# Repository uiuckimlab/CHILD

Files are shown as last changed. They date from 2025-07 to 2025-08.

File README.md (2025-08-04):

## Overview
For hardware details, please refer to the [BOM](./hardware/BOM.md).  
For software installation, please refer to [Teleop_Instruction](./Teleop_Instruction.md).
## To-Do
- \[ \] Release assembly guide.

## Citation
If you find this code useful in your research, please consider citing:
```
@article{child,
    title={CHILD (Controller for Humanoid Imitation and Live Demonstration): a Whole-Body Humanoid Teleoperation System}, 
    author={Noboru Myers and Obin Kwon and Sankalp Yamsani and Joohyung Kim},
    year={2025},
    journal={arXiv preprint arXiv:2508.00162},
    url={https://arxiv.org/abs/2508.00162}, 
}
```

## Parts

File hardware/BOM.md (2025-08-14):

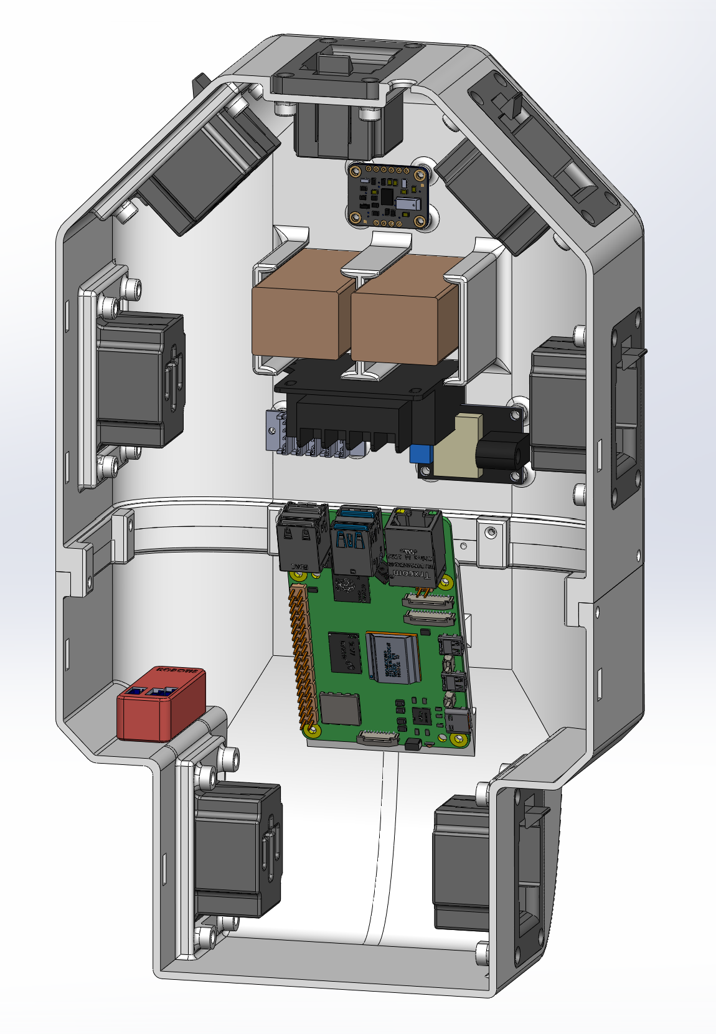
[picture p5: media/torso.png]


# Schematic
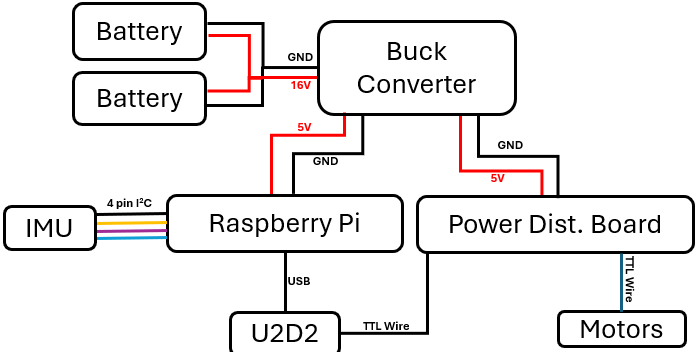
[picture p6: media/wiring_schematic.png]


# BOM
| Item | Quantity | Unit Cost (USD) | Cost | Source |  
| :--- | :---: | :---: | :---| :---|
| XL330-M288-T | 22 |  26.29 | 578.38 | [ROBOTIS](https://www.robotis.us/dynamixel-xl330-m288-t/)|
| XL330-M077-T | 2  |  26.29 | 52.58 | [ROBOTIS](https://www.robotis.us/dynamixel-xl330-m077-t/)|
| FPX330-H101 4pcs Set | 3  |  11.27 | 33.81 | [ROBOTIS](https://www.robotis.us/fpx330-h101-4pcs-set/)|
| Raspberry Pi 5a | 1  |  80 | 80 | [Digikey](https://www.digikey.com/en/products/detail/raspberry-pi/SC1112/21658257)|
| Raspberry Pi 5 active cooler | 1  |  9.50 | 9.50 | [Sparkfun](https://www.sparkfun.com/raspberry-pi-active-cooler.html?src=raspberrypi)|
| Buck converter | 1  |  11.00 | 11.00 | [Amazon](https://a.co/d/34K1G3W)|
| Lipo batteries | 2  |  31.49 | 62.98 | [getfpv](https://www.getfpv.com/batteries/mini-quad-batteries/lumenier-850mah-4s-75c-lipo-battery-xt-30.html)|
| IMU | 1  |  34.95 | 34.95 | [Adafruit](https://www.adafruit.com/product/2472)|
| U2D2 | 1  |  35.31 | 35.31 | [ROBOTIS](https://www.robotis.us/u2d2/?srsltid=AfmBOopnAfcYD4wZJd2mYGfl02LkN3lmzDXwg2oOkg-FG9G7V-jAIUyt)|
| TTL Expansion Board | 2  |  3.85 | 7.70 | [ROBOTIS](https://www.robotis.us/3p-extension-pcb/?searchid=199934&search_query=6+port+)|
| Baby Carrier | 1  |  37.99 | 37.99 | [Amazon](https://a.co/d/6YLBBi4)|
| XT30 Connector Female | 1  |  8.99 | 8.99 | [Amazon](https://a.co/d/beCXKoa)|
| SD card | 1  |  14.99 | 14.99 | [Amazon](https://a.co/d/bTOPJQl)|
| M3x8 screw | 33 |  0.0545 | 1.80 | [Mcmaster](https://www.mcmaster.com/91292A112/) |
| M2x8 screw | 4  |  0.0712 | 0.28 | [Mcmaster](https://www.mcmaster.com/91292a832/) |
| M2x6 screw | 24 |  0.0878 | 2.11 | [Mcmaster](https://www.mcmaster.com/91292a831/) |
| Female jumper wires | 6  |  0.0582 | 0.46 | [Amazon](https://a.co/d/gtiBsbT)|
| PLA Filament | 1.1kg  |  - | 25.3 | |
| | |  **Total** | 998.13 | |
### Miscellaneous
- Power wires

# Torso
**3D Prints**
- [leader_mount.STL](./3D_print_parts/leader_mount.STL) `x7`
- [back_cover_clip.STL](./3D_print_parts/back_cover_clip.STL) `x2`
- [back_cover_lower.STL](./3D_print_parts/back_cover_lower.STL)
- [back_cover_upper.STL](./3D_print_parts/back_cover_upper.STL)
- [torso_lower.STL](./3D_print_parts/torso_lower.STL)
- [torso_upper.STL](./3D_print_parts/torso_upper.STL)

# G1 Limb Leaders
Screws and wires for leader assembly (included in XL330 servo box):
- M2x6mm self tapping screw
- M2x8mm self tapping screw
- TTL wires

**3D Prints**
- [G1_Arm_Leader_R_handle.STL](./3D_print_parts/G1_Arm_Leader_R_handle.STL) `x2`
- [G1_Arm_Leader_trigger.STL](./3D_print_parts/G1_Arm_Leader_trigger.STL) `x2`
- [G1_Leg_Leader_foot.STL](./3D_print_parts/G1_Leg_Leader_foot.STL) `x2`
- [G1_Leg_Leader_knee_jnt_limit.STL](./3D_print_parts/G1_Leg_Leader_knee_jnt_limit.STL) `x2`
- [G1_Leg_Leader_link_2.STL](./3D_print_parts/G1_Leg_Leader_link_2.STL) `x2`
- [G1_Leg_Leader_link_3.STL](./3D_print_parts/G1_Leg_Leader_link_3.STL) `x2`
- [G1_Leg_Leader_link_4.1.STL](./3D_print_parts/G1_Leg_Leader_link_4.1.STL) `x2`
- [G1_Leg_Leader_link_4.2.STL](./3D_print_parts/G1_Leg_Leader_link_4.2.STL) `x2`
- [G1_Leg_Leader_L_link1.STL](./3D_print_parts/G1_Leg_Leader_L_link1.STL)
- [G1_Leg_Leader_R_link1.STL](./3D_print_parts/G1_Leg_Leader_R_link1.STL)
- [G1_Arm_Leader_L_link_1.STL](./3D_print_parts/G1_Arm_Leader_L_link_1.STL)
- [G1_Arm_Leader_L_link_2.STL](./3D_print_parts/G1_Arm_Leader_L_link_2.STL)
- [G1_Arm_Leader_L_link_3.STL](./3D_print_parts/G1_Arm_Leader_L_link_3.STL)
- [G1_Arm_Leader_L_link_4.STL](./3D_print_parts/G1_Arm_Leader_L_link_4.STL)
- [G1_Arm_Leader_L_link_5.STL](./3D_print_parts/G1_Arm_Leader_L_link_5.STL)
- [G1_Arm_Leader_L_link_6.STL](./3D_print_parts/G1_Arm_Leader_L_link_6.STL)
- [G1_Arm_Leader_R_link_1.STL](./3D_print_parts/G1_Arm_Leader_R_link_1.STL)
- [G1_Arm_Leader_R_link_2.STL](./3D_print_parts/G1_Arm_Leader_R_link_2.STL)
- [G1_Arm_Leader_R_link_3.STL](./3D_print_parts/G1_Arm_Leader_R_link_3.STL)
- [G1_Arm_Leader_R_link_4.STL](./3D_print_parts/G1_Arm_Leader_R_link_4.STL)
- [G1_Arm_Leader_R_link_5.STL](./3D_print_parts/G1_Arm_Leader_R_link_5.STL)
- [G1_Arm_Leader_R_link_6.STL](./3D_print_parts/G1_Arm_Leader_R_link_6.STL)

## Monitor Stand Adapter
- [Monitor_stand_attachment.STL](./3D_print_parts/Monitor_stand_attachment.STL)
- [Monitor_stand_bracket.STL](./3D_print_parts/Monitor_stand_bracket.STL)
- [monitor_stand_lock.STL](./3D_print_parts/monitor_stand_lock.STL)

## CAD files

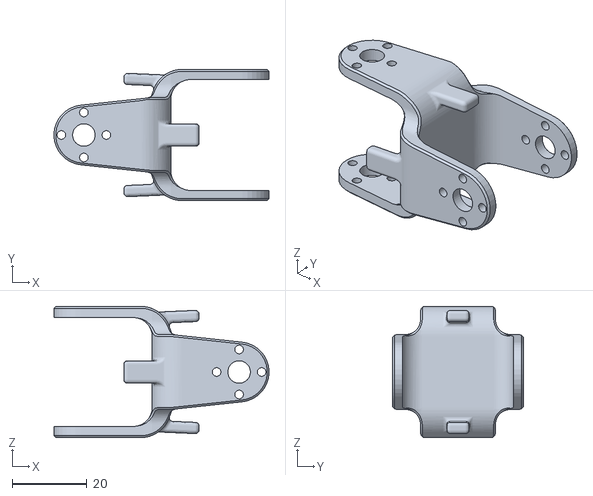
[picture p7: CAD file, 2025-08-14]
hardware/3D_print_parts/G1_Arm_Leader_L_link_6.STL
57.3 x 35.0 x 35.0

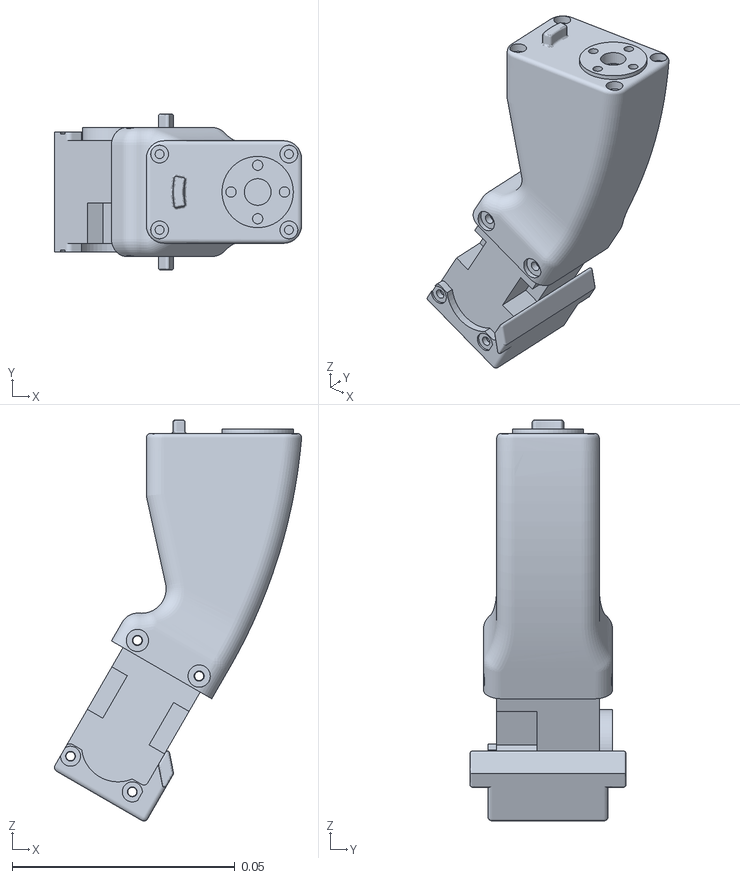
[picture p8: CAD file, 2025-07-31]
hw_interface/teleop_leaders/description/urdf/child_leaders/meshes/g1_leg_link_3.STL
0.0554 x 0.035 x 0.09

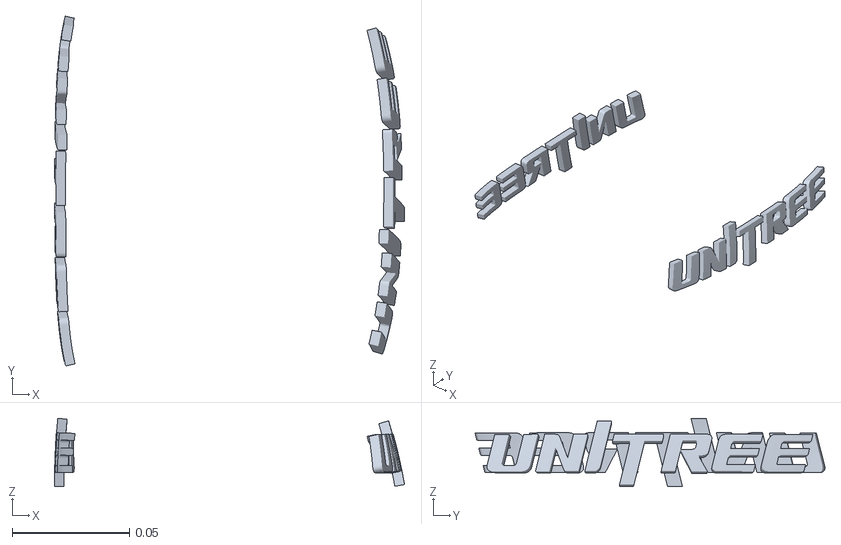
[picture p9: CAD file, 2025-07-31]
teleop_sw/models/assets/g1/meshes/logo_link.STL
0.149 x 0.149 x 0.0292

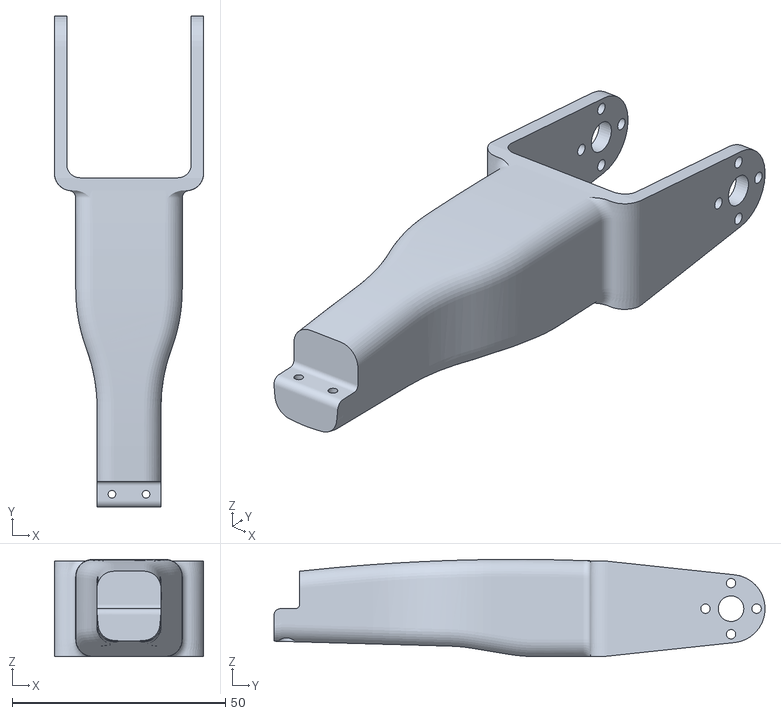
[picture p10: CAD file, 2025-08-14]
hardware/3D_print_parts/G1_Leg_Leader_link_4.1.STL
35.0 x 115.3 x 22.8

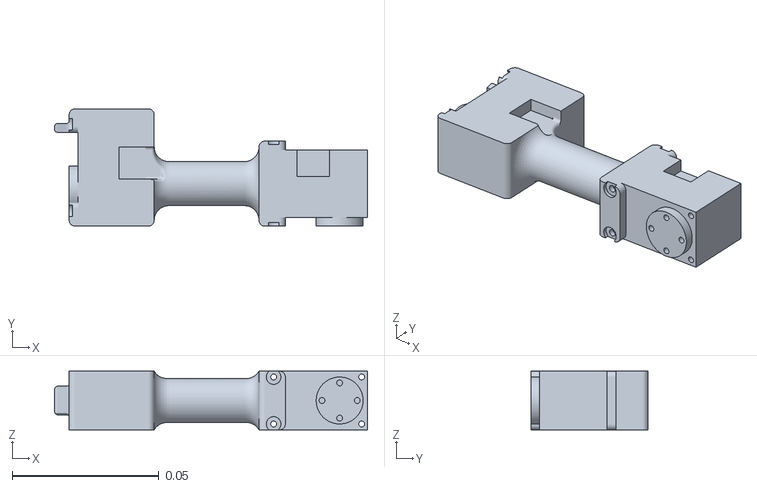
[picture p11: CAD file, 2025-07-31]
hw_interface/teleop_leaders/description/urdf/child_leaders/meshes/g1_arm_link_5_L.STL
0.107 x 0.04 x 0.02

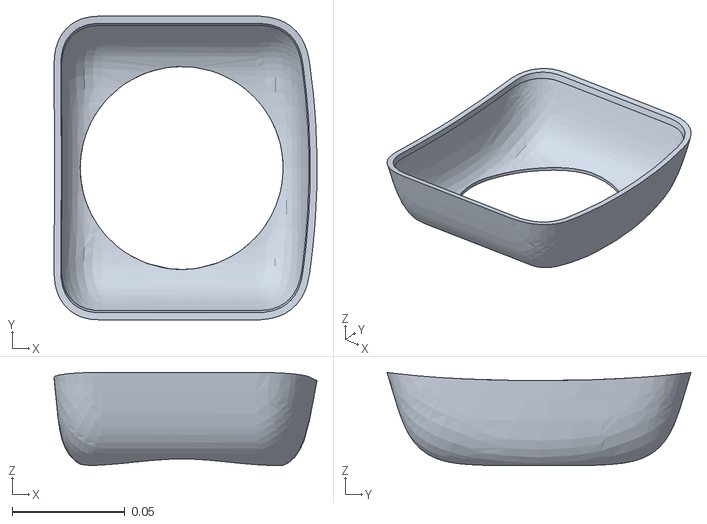
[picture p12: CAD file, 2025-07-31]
teleop_sw/models/assets/g1/meshes/waist_support_link.STL
0.117 x 0.135 x 0.0413

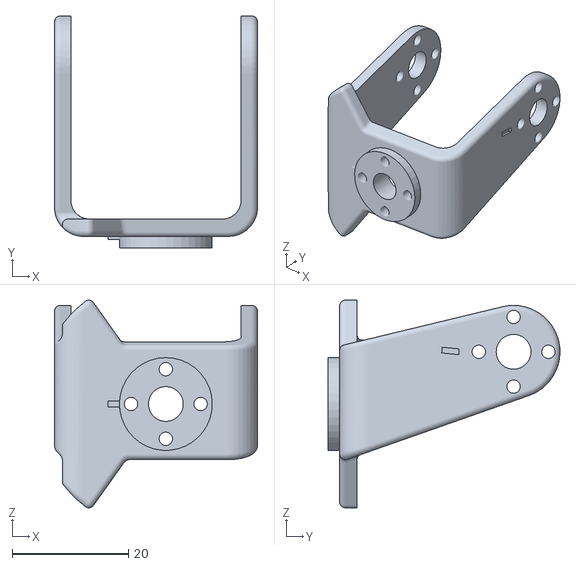
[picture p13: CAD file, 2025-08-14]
hardware/3D_print_parts/G1_Arm_Leader_L_link_4.STL
35.0 x 40.0 x 35.8

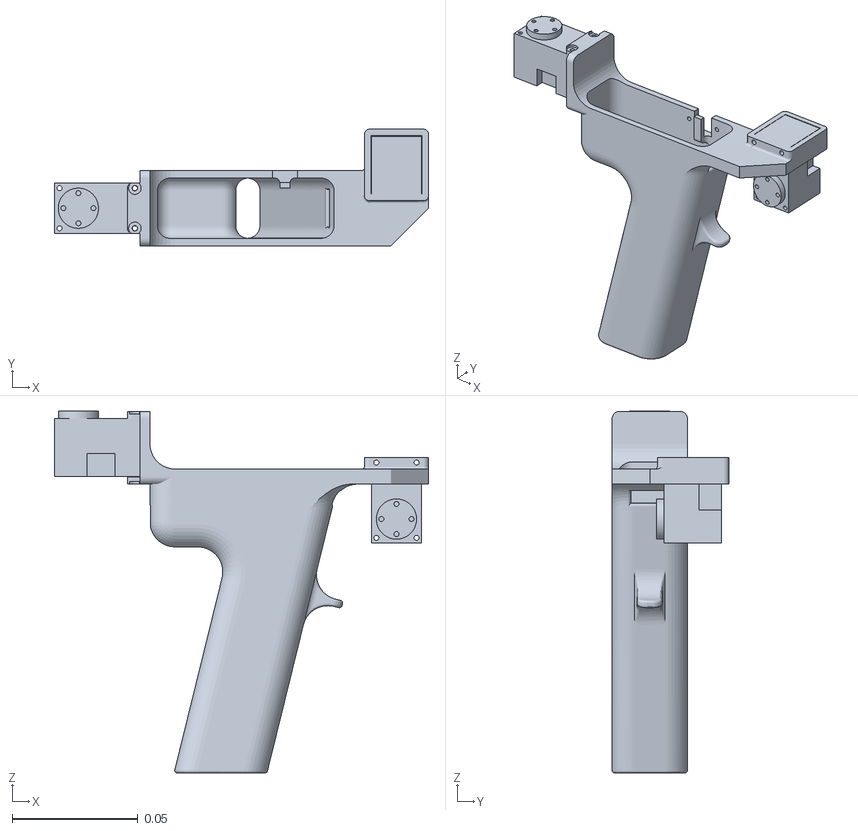
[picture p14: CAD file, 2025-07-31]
hw_interface/teleop_leaders/description/urdf/child_leaders/meshes/g1_arm_link_7_R.STL
0.149 x 0.0465 x 0.144

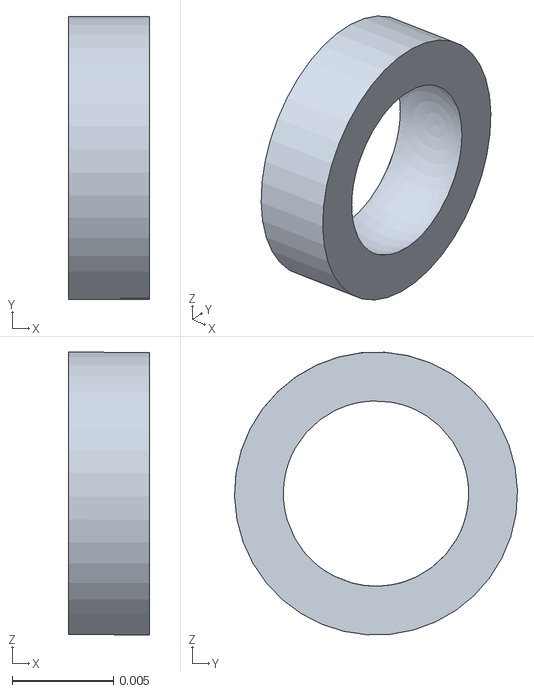
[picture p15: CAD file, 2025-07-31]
teleop_sw/models/assets/g1/meshes/torso_constraint_R_rod_link.STL
0.00401 x 0.014 x 0.014

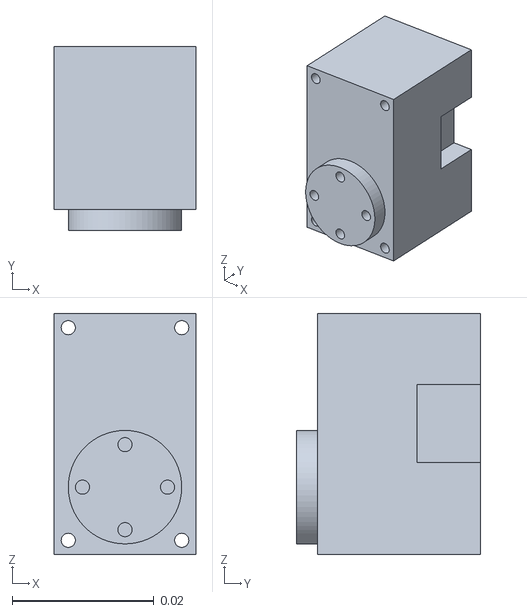
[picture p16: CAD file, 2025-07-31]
hw_interface/teleop_leaders/description/urdf/child_leaders/meshes/base_link_R.STL
0.02 x 0.026 x 0.034

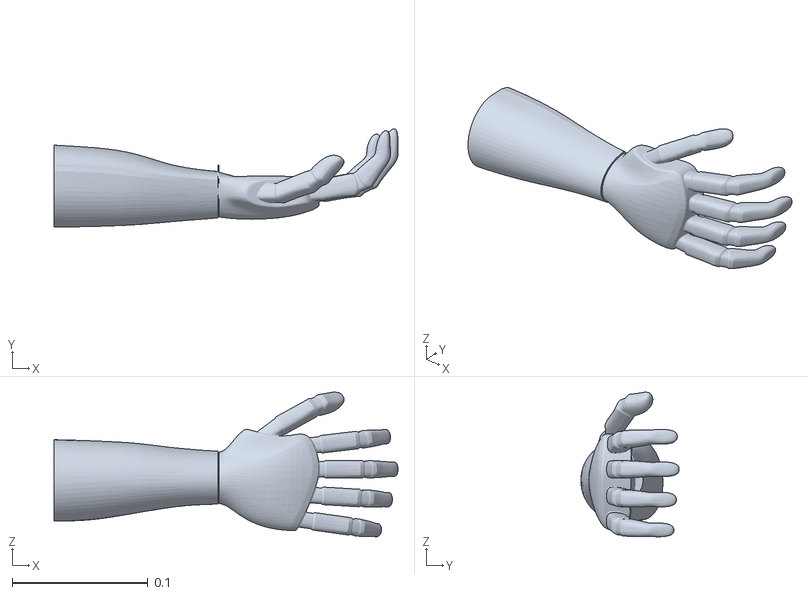
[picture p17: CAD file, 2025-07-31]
teleop_sw/models/assets/g1/meshes/right_wrist_roll_rubber_hand.STL
0.253 x 0.0724 x 0.106

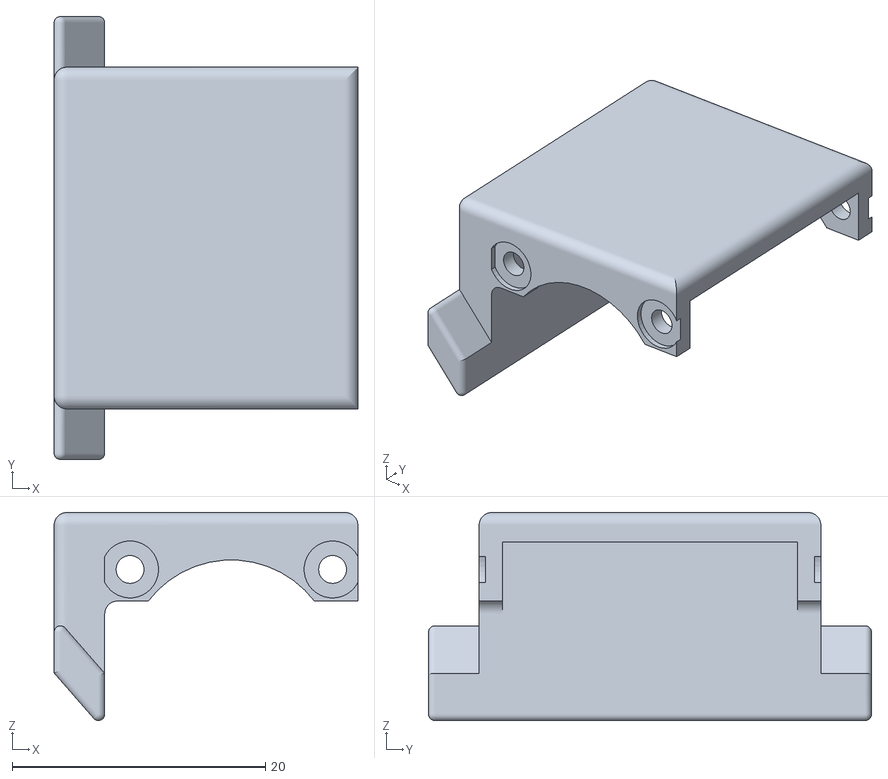
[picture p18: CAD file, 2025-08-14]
hardware/3D_print_parts/G1_Leg_Leader_knee_jnt_limit.STL
24.0 x 35.0 x 16.4

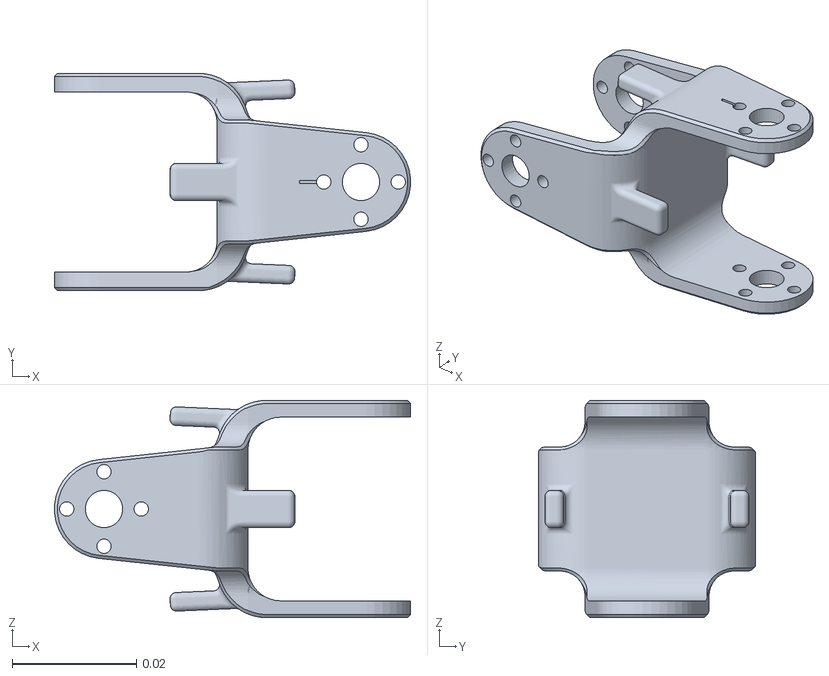
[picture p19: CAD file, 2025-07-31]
hw_interface/teleop_leaders/description/urdf/child_leaders/meshes/g1_arm_link_6_R.STL
0.0573 x 0.035 x 0.035

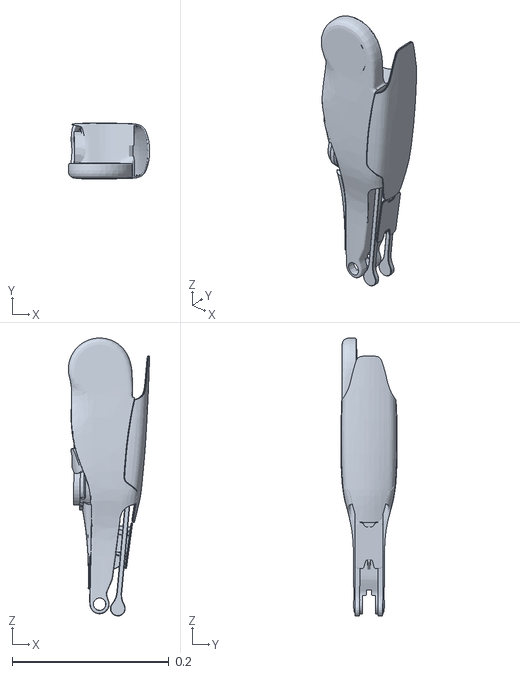
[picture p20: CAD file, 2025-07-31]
teleop_sw/models/assets/g1/meshes/right_knee_link.STL
0.104 x 0.0717 x 0.355

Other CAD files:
hardware/3D_print_parts/G1_Arm_Leader_R_link_6.STL
hardware/3D_print_parts/G1_Leg_Leader_L_link1.STL
hw_interface/teleop_leaders/description/urdf/child_leaders/meshes/base_link_L.STL
teleop_sw/models/assets/g1/meshes/right_hand_index_1_link.STL
hardware/3D_print_parts/G1_Arm_Leader_L_link_1.STL
hardware/3D_print_parts/G1_Arm_Leader_L_link_2.STL
hardware/3D_print_parts/G1_Arm_Leader_L_link_3.STL
hardware/3D_print_parts/G1_Arm_Leader_L_link_5.STL
hardware/3D_print_parts/G1_Arm_Leader_R_handle.STL
hardware/3D_print_parts/G1_Arm_Leader_R_link_1.STL
hardware/3D_print_parts/G1_Arm_Leader_R_link_2.STL
hardware/3D_print_parts/G1_Arm_Leader_R_link_3.STL
hardware/3D_print_parts/G1_Arm_Leader_R_link_4.STL
hardware/3D_print_parts/G1_Arm_Leader_R_link_5.STL
hardware/3D_print_parts/G1_Arm_Leader_trigger.STL
hardware/3D_print_parts/G1_Leg_Leader_R_link1.STL
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

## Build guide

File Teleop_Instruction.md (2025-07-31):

## Installation
### Inside CHILD
```
mkdir -p ws_child/src
cd ws_child/src
git clone https://github.com/uiuckimlab/CHILD.git
git clone https://github.com/uiuckimlab/PAPRAS-V0-Public.git -b ros2_humble
git clone -b humble https://github.com/ROBOTIS-GIT/DynamixelSDK.git
git clone -b humble https://github.com/ROBOTIS-GIT/dynamixel_interfaces.git
cd ../
colcon build --symlink-install
```

### Inside G1
- Setup ROS env
```
mkdir -p ws_child/src
cd ws_child/src
git clone https://github.com/uiuckimlab/CHILD.git
rm -r CHILD/hw_interface/teleop_leaders # for simple build
cd ../
colcon build --symlink-install
```
- Setup python virtualenv
```
cd ws_child/src/CHILD
virtualenv venv_child -p python3.8
source venv_child/bin/activate
cd teleop_sw
pip install -r requirements.txt
```
If pip install shows "ERROR: could not find a version that satisfies the requirement libxml2" run:
```
pip install lxml --only-binary :all:
pip install -r requirements.txt
```
Install unitree_sdk2_python from source
```
git clone https://github.com/unitreerobotics/unitree_sdk2_python.git
cd unitree_sdk2_python
pip3 install -e .
```
Update the IP addresses on lines 11 and 12 of the cycloneds.xml file to match G1 and CHILD
```
<Peer address="xx.x.xx.xxx"/>
<Peer address="xx.x.xx.xxx"/>
```

# Robot Setup



Also this is an official doc for booting up and making G1 to stand:

https://support.unitree.com/home/en/G1_developer/quick_start

### Standing & Walking Mode

0. After booting up the robot, the robot will be in `Zero Torque` mode.
1. Press `L2+B` then the robot will be in `Damping` mode in `Normal` mode. At this step, if you raise the robot arm, you can feel the torque from the shoulder joint.
2. Press `L2+Up`, the robot will be in `Get Ready`, and arms will go to specific pose. Now you can put g1 down to the ground.
3. Press `R1+Y`  it goes to `Main Operation Control` mode, it will starts to try balancing
4. If you press `R2+A` instead of `R1+Y`, it will goes to `Runninng Mode`. The robot will walk a lot faster. You can increase/decrease the velocity using `R2+Down` or `R2+Up`.

- **E-STOP**:  Hold `L2+B` for 5 seconds

### Debug Mode

0. After booting up the robot, the robot will be in `Zero Torque` mode.
1. Press `L2+R2` then the robot will be in `Damping` mode in `Debug` mode. At this step, if you raise the robot arm, you can feel the torque from the shoulder joint.
2. Press `L2+A`, the robot will be in `Diagnostic Action`, and arms will go to specific pose. 
3. G1 is ready for teleoperation!

## Teleop Setup

- If you want both walking&teleop, make G1 to stand on the ground before running teleop codes.

### Inside CHILD

```
export CHILD_WIFI_ADDRESS=XX.X.XX.XXX
ssh papras@$CHILD_WIFI_ADDRESS
```
- launch ros2 docker 

    - `docker ps -a` : To see the list of existing container

    - If there is a container with name `ros_humble`

        - ```
            docker start ros_humble && docker exec -it ros_humble bash
            ```

    - If there is not, 

      ```shell
        docker run -it --privileged -v /dev/bus/usb:/dev/bus/usb --env=DISPLAY --volume="/etc/group:/etc/group:ro" --volume="/etc/passwd:/etc/passwd:ro" --volume="/etc/shadow:/etc/shadow:ro" --volume="/etc/sudoers.d:/etc/sudoers.d:ro" --net host -v /home:/home -v ~/Docker/hosts:/etc/hosts -v ~/shared:/home/usr/ papras-ros-humble
      ```

- Setup ROS env

  ```shell
  cd /home/papras/shared/ws_child/ && source install/setup.bash
  export ROS_DOMAIN_ID=55
  ros2 launch teleop_leaders leader_hw_g1_all_limbs.launch.py 
  ```

### Inside G1

- Make sure G1 is connected to the same wifi as CHILD.

- - If g1 is not connected to wifi, wire-connect to g1, and 

    ```
    ssh unitree@192.168.123.164
    sudo nmcli connection up <wifi-name>
    ```
```
export G1_WIFI_ADDRESS=10.1.10.189 # Please replace this IP address with your G1's IP address
ssh -X unitree@$G1_WIFI_ADDRESS
```
- for the teleop demo with baby, enter followings (If using a different ROS domain ID, must modify line 2 of cyclonedds.xml before exporting)
```
export CYCLONEDDS_URI=file:///home/unitree/ws_child/src/CHILD/teleop_sw/cyclonedds.xml
export ROS_DOMAIN_ID=55
cd ws_child
source install/setup.bash
cd src/CHILD
source venv_child/bin/activate
cd teleop_sw
python -m run_g1_upper_body # for upper body control - need to be in standing mode
python -m run_g1_full_body_teleop # for whole body control - need to be in debug mode
```

- It will have multiple stages to start teleoperation
    0. G1 will go to the zero pose
    1. Pressing both gripper 3 secs, it will go to the initial pose from the baby
    2. Then teleoperation starts.
    3. If the operator press one of the gripper 2 secs, the leg on the same side will be activated.
       - The leg can be used as joystick for walking
       - If both of the legs are activated, the speed and orientation are the sum of the values from each leg.
       - if the operator press the gripper 2secs while activated, the leg will go back to deactivated mode -> zero position.
    4. If the operator press both of the grippers 3 secs, the teleoperation will be ended.

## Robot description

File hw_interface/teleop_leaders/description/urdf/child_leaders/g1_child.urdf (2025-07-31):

<?xml version="1.0" ?>
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
<robot name="g1_Light_arm_leader">
    <mujoco>
       <compiler angle="radian" meshdir="./" autolimits="true" strippath="false" fusestatic="false"/>
    </mujoco>
  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
  <link name="left_arm_base_link">
    <inertial>
      <origin rpy="0 0 0" xyz="0.00000000 -0.01230125 0.00718113"/>
      <mass value="0.01800000"/>
      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
    </inertial>
    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
  </link>
  <link name="left_arm_link1">
    <inertial>
      <origin rpy="0 0 0" xyz="0.01387236 0.00000000 0.00000273"/>
      <mass value="0.00630282"/>
      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
    </inertial>
    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
  </link>
  <link name="left_arm_link2">
    <inertial>
      <origin rpy="0 0 0" xyz="0 -0.00345697 -0.00992158"/>
      <mass value="0.02099123"/>
      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
    </inertial>
    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
  </link>
  <link name="left_arm_link3">
    <inertial>
      <origin rpy="0 0 0" xyz="-0.00311665 0.00003705 -0.0729065"/>
      <mass value="0.06865114"/>
      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
    </inertial>
    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
  </link>
  <link name="left_arm_link4">
    <inertial>
      <origin rpy="0 0 0" xyz="0.01902443 0.00064065 -0.00588890"/>
      <mass value="0.00704644"/>
      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
    </inertial>
    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
  </link>
  <link name="left_arm_link5">
    <inertial>
      <origin rpy="0 0 0" xyz="0.04583889 -0.00415733 0.00000000"/>
      <mass value="0.05392167"/>
      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
    </inertial>
    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
  </link>
  <link name="left_arm_link6">
    <inertial>
      <origin rpy="0 0 0" xyz="0.02038055 -0.00000138 -0.00000112"/>
      <mass value=" 0.01167564"/>
      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
    </inertial>
    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
  </link>
  <link name="left_arm_link7">
    <inertial>
      <origin rpy="0 0 0" xyz="0.06890215 0.00304461 -0.04175166"/>
      <mass value="0.1095606"/>
      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
    </inertial>
    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
  </link>
  <joint name="left_shoulder_pitch_joint" type="revolute">
    <origin rpy="0 0 -3.1415926535" xyz="0 0.026 0"/>
    <parent link="left_arm_base_link"/>
    <child link="left_arm_link1"/>
    <axis xyz="0 -1 0"/>
    <limit effort="0" lower="-3.0892" upper="2.6704" velocity="1.0"/>
  </joint>
  <joint name="left_shoulder_roll_joint" type="revolute">
    <origin rpy="0 0 3.1415926" xyz="-0.00415 -0.03339492 0"/>
    <parent link="left_arm_link1"/>
    <child link="left_arm_link2"/>
    <axis xyz="1 0 0"/>
    <limit effort="0" lower="-1.5882" upper="2.2515" velocity="1.0"/>
  </joint>
  <joint name="left_shoulder_yaw_joint" type="revolute">
    <origin rpy="0 0 0" xyz="-0.009766 0 -0.031"/>
    <parent link="left_arm_link2"/>
    <child link="left_arm_link3"/>
    <axis xyz="0 0 1"/>
    <limit effort="0" lower="-2.618" upper="2.618" velocity="1.0"/>
  </joint>
  <joint name="left_elbow_joint" type="revolute">
    <origin rpy="0 0 0" xyz="0.0142047 0 -0.1343462"/>
    <parent link="left_arm_link3"/>
    <child link="left_arm_link4"/>
    <axis xyz="0 1 0"/>
    <limit effort="0" lower="-1.0472" upper="2.0944" velocity="1.0"/>
  </joint>
  <joint name="left_wrist_roll_joint" type="revolute">
    <origin rpy="0 0 0" xyz="0.032 -0.001699119 -0.009"/>
    <parent link="left_arm_link4"/>
    <child link="left_arm_link5"/>
    <axis xyz="1 0 0"/>
    <limit effort="0" lower="-1.972222054" upper="1.972222054" velocity="1.0"/>
  </joint>
  <joint name="left_wrist_pitch_joint" type="revolute">
    <origin rpy="0 0 0" xyz="0.09205 -0.00185 0"/>
    <parent link="left_arm_link5"/>
    <child link="left_arm_link6"/>
    <axis xyz="0 1 0"/>
    <limit effort="0" lower="-1.614429558" upper="1.614429558" velocity="1.0"/>
  </joint>
  <joint name="left_wrist_yaw_joint" type="revolute">
    <origin rpy="0 0 0" xyz="0.0414 0 0.0043"/>
    <parent link="left_arm_link6"/>
    <child link="left_arm_link7"/>
    <axis xyz="0 0 1"/>
    <limit effort="0" lower="-1.614429558" upper="1.614429558" velocity="1.0"/>
  </joint>
  <link name="right_arm_base_link">
    <inertial>
      <origin rpy="0 0 0" xyz="0.00000000 -0.01230125 0.00718113"/>
      <mass value="0.01800000"/>
      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
    </inertial>
    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
  </link>
  <link name="right_arm_link1">
    <inertial>
      <origin rpy="0 0 0" xyz="0.01387236 0.00000000 0.00000273"/>
      <mass value="0.00630282"/>
      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
    </inertial>
    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
  </link>
  <link name="right_arm_link2">
    <inertial>
      <origin rpy="0 0 0" xyz="0 -0.00345697 -0.00992158"/>
      <mass value="0.02099123"/>
      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
    </inertial>
    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
  </link>
  <link name="right_arm_link3">
    <inertial>
      <origin rpy="0 0 0" xyz="-0.00311665 0.00003705 -0.0729065"/>
      <mass value="0.06865114"/>
      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
    </inertial>
    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
  </link>
  <link name="right_arm_link4">
    <inertial>
      <origin rpy="0 0 0" xyz="0.01902443 0.00064065 -0.00588890"/>
      <mass value="0.00704644"/>
      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
    </inertial>
    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
  </link>
  <link name="right_arm_link5">
    <inertial>
      <origin rpy="0 0 0" xyz="0.04583889 -0.00415733 0.00000000"/>
      <mass value="0.05392167"/>
      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
    </inertial>
    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
  </link>
  <link name="right_arm_link6">
    <inertial>
      <origin rpy="0 0 0" xyz="0.02038055 -0.00000138 -0.00000112"/>
      <mass value=" 0.01167564"/>
      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
    </inertial>
    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
  </link>
  <link name="right_arm_link7">
    <inertial>
      <origin rpy="0 0 0" xyz="0.06890215 0.00304461 -0.04175166"/>
      <mass value="0.1095606"/>
      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
    </inertial>
    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
  </link>
  <joint name="right_shoulder_pitch_joint" type="revolute">
    <origin rpy="0 0 0" xyz="0 -0.026 0"/>
    <parent link="right_arm_base_link"/>
    <child link="right_arm_link1"/>
    <axis xyz="0 1 0"/>
    <limit effort="0" lower="-3.0892" upper="2.6704" velocity="1.0"/>
  </joint>
  <joint name="right_shoulder_roll_joint" type="revolute">
    <origin rpy="0 0 0" xyz="0.00415 -0.03339492 0"/>
    <parent link="right_arm_link1"/>
    <child link="right_arm_link2"/>
    <axis xyz="1 0 0"/>
    <limit effort="0" lower="-2.2515" upper="1.5882" velocity="1.0"/>
  </joint>
  <joint name="right_shoulder_yaw_joint" type="revolute">
    <origin rpy="0 0 0" xyz="-0.009766 0 -0.031"/>
    <parent link="right_arm_link2"/>
    <child link="right_arm_link3"/>
    <axis xyz="0 0 1"/>
    <limit effort="0" lower="-2.618" upper="2.618" velocity="1.0"/>
  </joint>
  <joint name="right_elbow_joint" type="revolute">
    <origin rpy="0 0 0" xyz="0.0142047 0 -0.1343462"/>
    <parent link="right_arm_link3"/>
    <child link="right_arm_link4"/>
    <axis xyz="0 1 0"/>
    <limit effort="0" lower="-1.0472" upper="2.0944" velocity="1.0"/>
  </joint>
  <joint name="right_wrist_roll_joint" type="revolute">
    <origin rpy="0 0 0" xyz="0.032 -0.001699119 -0.009"/>
    <parent link="right_arm_link4"/>
    <child link="right_arm_link5"/>
    <axis xyz="1 0 0"/>
    <limit effort="0" lower="-1.972222054" upper="1.972222054" velocity="1.0"/>
  </joint>
  <joint name="right_wrist_pitch_joint" type="revolute">
    <origin rpy="0 0 0" xyz="0.09205 -0.00185 0"/>
    <parent link="right_arm_link5"/>
    <child link="right_arm_link6"/>
    <axis xyz="0 1 0"/>
    <limit effort="0" lower="-1.614429558" upper="1.614429558" velocity="1.0"/>
  </joint>
  <joint name="right_wrist_yaw_joint" type="revolute">
    <origin rpy="0 0 0" xyz="0.0414 0 0.0043"/>
    <parent link="right_arm_link6"/>
    <child link="right_arm_link7"/>
    <axis xyz="0 0 1"/>
    <limit effort="0" lower="-1.614429558" upper="1.614429558" velocity="1.0"/>
  </joint>
  <link name="left_leg_base_link">
    <inertial>
      <origin rpy="0 0 0" xyz="0.00000000 0.00319875 0.00118113"/>
      <mass value="0.01800000"/>
      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
    </inertial>
    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
  </link>
  <link name="left_leg_link1">
    <inertial>
      <origin rpy="0 0 0" xyz="0.01016296 0.00000000 -0.00475105"/>
      <mass value="0.00543603"/>
      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
    </inertial>
    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
  </link>
  <link name="left_leg_link2">
    <inertial>
      <origin rpy="0 0 0" xyz="-0.00272858 0.00000000 -0.02683543"/>
      <mass value=" 0.04516848"/>
      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
    </inertial>
    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
  </link>
  <link name="left_leg_link3">
    <inertial>
      <origin rpy="0 0 0" xyz="-0.01621315 0.00022419 -0.04019605"/>
      <mass value=" 0.06431956"/>
      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
    </inertial>
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

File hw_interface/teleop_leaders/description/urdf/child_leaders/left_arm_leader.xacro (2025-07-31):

<?xml version="1.0" encoding="utf-8"?>
<robot xmlns:xacro="http://www.ros.org/wiki/xacro" name="g1_Light_arm_leader">

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
  <link name="left_arm_base_link">
    <inertial>
      <origin xyz="0.00000000 -0.01230125 0.00718113" rpy="0 0 0" />
      <mass value="0.01800000" />
      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
    </inertial>
    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
  </link>  


  <link name="left_arm_link1">
    <inertial>
      <origin xyz="0.01387236 0.00000000 0.00000273" rpy="0 0 0" />
      <mass value="0.00630282" />
      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
    </inertial>
    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
  </link> 

  <link name="left_arm_link2">
    <inertial>
      <origin xyz="0 -0.00345697 -0.00992158" rpy="0 0 0" />
      <mass value="0.02099123" />
      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
    </inertial>
    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
  </link>

  <link name="left_arm_link3">
    <inertial>
      <origin xyz="-0.00311665 0.00003705 -0.0729065" rpy="0 0 0" />
      <mass value="0.06865114" />
      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
    </inertial>
    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
  </link>
  <link name="left_arm_link4">
    <inertial>
      <origin xyz="0.01902443 0.00064065 -0.00588890" rpy="0 0 0" />
      <mass value="0.00704644" />
      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
    </inertial>
    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
  </link>
 
  <link name="left_arm_link5">
    <inertial>
      <origin xyz="0.04583889 -0.00415733 0.00000000" rpy="0 0 0" />
      <mass value="0.05392167" />
      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
    </inertial>
    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
  </link>
 
  <link name="left_arm_link6">
    <inertial>
      <origin xyz="0.02038055 -0.00000138 -0.00000112" rpy="0 0 0" />
      <mass value=" 0.01167564" />
      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
    </inertial>
    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
  </link> 
  <link name="left_arm_link7">
    <inertial>
      <origin xyz="0.06890215 0.00304461 -0.04175166" rpy="0 0 0" />
      <mass value="0.1095606" />
      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
    </inertial>
    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
  </link>  



  <joint name="left_shoulder_pitch_joint" type="revolute">
    <origin xyz="0 0.026 0" rpy="0 0 -3.1415926535" />
    <parent link="left_arm_base_link" />
    <child link="left_arm_link1" />
    <axis xyz="0 -1 0" />
    <limit lower="-3.0892" upper="2.6704" effort="0" velocity="1.0" />
  </joint>
  
  <joint name="left_shoulder_roll_joint" type="revolute">
    <origin xyz="-0.00415 -0.03339492 0" rpy="0 0 3.1415926" />
    <parent link="left_arm_link1" />
    <child link="left_arm_link2" />
    <axis xyz="1 0 0" />
    <limit lower="-1.5882" upper="2.2515" effort="0" velocity="1.0" />
  </joint>
  
  <joint name="left_shoulder_yaw_joint" type="revolute">
    <origin xyz="-0.009766 0 -0.031" rpy="0 0 0" />
    <parent link="left_arm_link2" />
    <child link="left_arm_link3" />
    <axis xyz="0 0 1" />
    <limit lower="-2.618" upper="2.618" effort="0" velocity="1.0" />
  </joint>
  
  <joint name="left_elbow_joint" type="revolute">
    <origin xyz="0.0142047 0 -0.1343462" rpy="0 0 0" />
    <parent link="left_arm_link3" />
    <child link="left_arm_link4" />
    <axis xyz="0 1 0" />
    <limit lower="-1.0472" upper="2.0944" effort="0" velocity="1.0" />
  </joint>
  
  <joint name="left_wrist_roll_joint" type="revolute">
    <origin xyz="0.032 -0.001699119 -0.009" rpy="0 0 0" />
    <parent link="left_arm_link4" />
    <child link="left_arm_link5" />
    <axis xyz="1 0 0" />
    <limit lower="-1.972222054" upper="1.972222054" effort="0" velocity="1.0" />
  </joint>
  
  <joint name="left_wrist_pitch_joint" type="revolute">
    <origin xyz="0.09205 -0.00185 0" rpy="0 0 0" />
    <parent link="left_arm_link5" />
    <child link="left_arm_link6" />
    <axis xyz="0 1 0" />
    <limit lower="-1.614429558" upper="1.614429558" effort="0" velocity="1.0" />
  </joint>

  <joint name="left_wrist_yaw_joint" type="revolute">
    <origin xyz="0.0414 0 0.0043" rpy="0 0 0" />
    <parent link="left_arm_link6" />
    <child link="left_arm_link7" />
    <axis xyz="0 0 1" />
    <limit lower="-1.614429558" upper="1.614429558" effort="0" velocity="1.0" />
  </joint>
</robot>

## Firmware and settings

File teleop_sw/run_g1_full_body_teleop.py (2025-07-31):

import os
import numpy as np
import time
import time
import sys

from unitree_sdk2py.core.channel import ChannelPublisher, ChannelFactoryInitialize
from unitree_sdk2py.core.channel import ChannelSubscriber#, ChannelFactoryInitialize
from unitree_sdk2py.idl.default import unitree_hg_msg_dds__LowCmd_
from unitree_sdk2py.idl.default import unitree_hg_msg_dds__LowState_
from unitree_sdk2py.idl.unitree_hg.msg.dds_ import LowCmd_
from unitree_sdk2py.idl.unitree_hg.msg.dds_ import LowState_
from unitree_sdk2py.utils.crc import CRC
from unitree_sdk2py.utils.thread import RecurrentThread
from unitree_sdk2py.comm.motion_switcher.motion_switcher_client import MotionSwitcherClient
from configs.default import BaseConfig
robot_config, device_config = BaseConfig().parse()
from tqdm import tqdm
from omegaconf import OmegaConf
from src.devices import DEVICES_DICT

kPi = 3.141592654
kPi_2 = 1.57079632
class Mode:
    PR = 0  # Series Control for Pitch/Roll Joints
    AB = 1  # Parallel Control for A/B Joints
USE_WAIST = False
class G1JointIndex:
    # Left leg
    LeftHipPitch = 0
    LeftHipRoll = 1
    LeftHipYaw = 2
    LeftKnee = 3
    LeftAnklePitch = 4
    LeftAnkleB = 4
    LeftAnkleRoll = 5
    LeftAnkleA = 5

    # Right leg
    RightHipPitch = 6
    RightHipRoll = 7
    RightHipYaw = 8
    RightKnee = 9
    RightAnklePitch = 10
    RightAnkleB = 10
    RightAnkleRoll = 11
    RightAnkleA = 11

    WaistYaw = 12
    WaistRoll = 13        # NOTE: INVALID for g1 23dof/29dof with waist locked
    WaistA = 13           # NOTE: INVALID for g1 23dof/29dof with waist locked
    WaistPitch = 14       # NOTE: INVALID for g1 23dof/29dof with waist locked
    WaistB = 14           # NOTE: INVALID for g1 23dof/29dof with waist locked

    # Left arm
    LeftShoulderPitch = 15
    LeftShoulderRoll = 16
    LeftShoulderYaw = 17
    LeftElbow = 18
    LeftWristRoll = 19
    LeftWristPitch = 20   # NOTE: INVALID for g1 23dof
    LeftWristYaw = 21     # NOTE: INVALID for g1 23dof

    # Right arm
    RightShoulderPitch = 22
    RightShoulderRoll = 23
    RightShoulderYaw = 24
    RightElbow = 25
    RightWristRoll = 26
    RightWristPitch = 27  # NOTE: INVALID for g1 23dof
    RightWristYaw = 28    # NOTE: INVALID for g1 23dof

    kNotUsedJoint = 29 # NOTE: Weight

child = DEVICES_DICT[device_config.type](robot_config, device_config)
class Runner():
    def __init__(self, device_config):
        self.child = child
        self.child.launch_init(np.zeros(14))
        self.shutdown = False

        self.time_ = 0.0
        self.control_dt_ = 0.01
        self.duration_ = 6.0
        self.counter_ = 0
        self.weight = 0.
        self.weight_rate = 0.2
        self.kp = 60.
        self.kd = 1.0
        self.dq = 0.
        self.tau_ff = 0.
        self.mode_machine_ = 0
        self.low_cmd = unitree_hg_msg_dds__LowCmd_()
        self.low_state = None
        self.first_update_low_state = False
        self.crc = CRC()
        self.done = False
        self.prev_target_qpos = None
        self.mode_machine_ = 0
        self.joints = [
          G1JointIndex.LeftHipPitch,G1JointIndex.LeftHipRoll,
          G1JointIndex.LeftHipYaw,G1JointIndex.LeftKnee,
          G1JointIndex.RightHipPitch,G1JointIndex.RightHipRoll,
          G1JointIndex.RightHipYaw,G1JointIndex.RightKnee,
          G1JointIndex.LeftShoulderPitch,  G1JointIndex.LeftShoulderRoll,
          G1JointIndex.LeftShoulderYaw,    G1JointIndex.LeftElbow,
          G1JointIndex.LeftWristRoll,      G1JointIndex.LeftWristPitch,
          G1JointIndex.LeftWristYaw,
          G1JointIndex.RightShoulderPitch, G1JointIndex.RightShoulderRoll,
          G1JointIndex.RightShoulderYaw,   G1JointIndex.RightElbow,
          G1JointIndex.RightWristRoll,     G1JointIndex.RightWristPitch,
          G1JointIndex.RightWristYaw,
          G1JointIndex.WaistYaw,
          G1JointIndex.WaistRoll,
          G1JointIndex.WaistPitch
        ]

        self.idx_mapping_dict = {
            'left_hip_pitch_joint': G1JointIndex.LeftHipPitch,
            'left_hip_roll_joint': G1JointIndex.LeftHipRoll,
            'left_hip_yaw_joint': G1JointIndex.LeftHipYaw,
            'left_knee_joint': G1JointIndex.LeftKnee,
            'left_ankle_pitch_joint': G1JointIndex.LeftAnklePitch,
            'left_ankle_roll_joint': G1JointIndex.LeftAnkleRoll,
            'right_hip_pitch_joint': G1JointIndex.RightHipPitch,
            'right_hip_roll_joint': G1JointIndex.RightHipRoll,
            'right_hip_yaw_joint': G1JointIndex.RightHipYaw,
            'right_knee_joint': G1JointIndex.RightKnee,
            'right_ankle_pitch_joint': G1JointIndex.RightAnklePitch,
            'right_ankle_roll_joint': G1JointIndex.RightAnkleRoll,
            'left_shoulder_pitch_joint':  G1JointIndex.LeftShoulderPitch,
            'left_shoulder_roll_joint': G1JointIndex.LeftShoulderRoll,
            'left_shoulder_yaw_joint': G1JointIndex.LeftShoulderYaw,
            'left_elbow_joint': G1JointIndex.LeftElbow,
            'left_wrist_roll_joint': G1JointIndex.LeftWristRoll,
            'left_wrist_pitch_joint': G1JointIndex.LeftWristPitch,
            'left_wrist_yaw_joint': G1JointIndex.LeftWristYaw,
            'right_shoulder_pitch_joint': G1JointIndex.RightShoulderPitch,
            'right_shoulder_roll_joint': G1JointIndex.RightShoulderRoll,
            'right_shoulder_yaw_joint': G1JointIndex.RightShoulderYaw,
            'right_elbow_joint': G1JointIndex.RightElbow,
            'right_wrist_roll_joint': G1JointIndex.RightWristRoll,
            'right_wrist_pitch_joint': G1JointIndex.RightWristPitch,
            'right_wrist_yaw_joint': G1JointIndex.RightWristYaw
            #waist_yaw_joint':G1JointIndex.WaistYaw
            # add for waist
        }

        self.waist_ind_array = [
            G1JointIndex.WaistPitch,
            G1JointIndex.WaistRoll,
            G1JointIndex.WaistYaw,
        ]

        self.child2g1_idx_mapping_array, self.g12child_idx_mapping_dict = [], {}
        id = 0
        for limb_name, limb_joint_names in device_config.limb_joint_names.items():
            for joint_name in limb_joint_names:
                joint_idx = self.idx_mapping_dict[joint_name]
                self.child2g1_idx_mapping_array.append(joint_idx)
                self.g12child_idx_mapping_dict[joint_idx] = id
                id += 1

        self.kp_dict = {joint_idx: self.kp for joint_idx in self.child2g1_idx_mapping_array}
        for waist_joint in self.waist_ind_array:
            self.kp_dict[waist_joint] = 200

        self.kd_dict = {joint_idx: self.kd for joint_idx in self.child2g1_idx_mapping_array}
        for waist_joint in self.waist_ind_array:
            self.kd_dict[waist_joint] = 5

        self.kp_dict[G1JointIndex.LeftWristPitch] = 10.0
        self.kp_dict[G1JointIndex.RightWristPitch] = 10.0
        self.kp_dict[G1JointIndex.LeftWristRoll] = 10.0
        self.kp_dict[G1JointIndex.RightWristRoll] = 10.0
        self.kp_dict[G1JointIndex.LeftWristYaw] = 5.0
        self.kp_dict[G1JointIndex.RightWristYaw] = 5.0

        self.kd_dict[G1JointIndex.LeftWristPitch] = 0.5
        self.kd_dict[G1JointIndex.RightWristPitch] = 0.5
        self.kd_dict[G1JointIndex.LeftWristRoll] = 0.5
        self.kd_dict[G1JointIndex.RightWristRoll] = 0.5
        self.kd_dict[G1JointIndex.LeftWristYaw] = 0.5
        self.kd_dict[G1JointIndex.RightWristYaw] = 0.5




        self.update_mode_machine_ = False


    def Init(self):

        self.msc = MotionSwitcherClient()
        self.msc.SetTimeout(5.0)
        self.msc.Init()

        status, result = self.msc.CheckMode()
        while result['name']:
            self.msc.ReleaseMode()
            status, result = self.msc.CheckMode()
            time.sleep(1)
        # create publisher #
        self.arm_sdk_publisher = ChannelPublisher("rt/lowcmd", LowCmd_)
        self.arm_sdk_publisher.Init()

        # create subscriber #
        self.lowstate_subscriber = ChannelSubscriber("rt/lowstate", LowState_)
        self.lowstate_subscriber.Init(self.LowStateHandler, 10)

        while self.first_update_low_state == False:
            print("trying to get low state")
            time.sleep(1)
        print("Got low_state")


    def LowStateHandler(self, msg: LowState_):
        self.low_state = msg
        self.first_update_low_state = True
        if self.update_mode_machine_ == False:
            self.mode_machine_ = self.low_state.mode_machine
            self.update_mode_machine_ = True
        
        self.counter_ +=1
        if (self.counter_ % 500 == 0) :
            self.counter_ = 0


    def run(self):

        ## Phase1: Initialize the limbs to zero pose
        zero_duration = 3.0
        time_ = 0
        pbar = tqdm(total=int(zero_duration/self.control_dt_), desc='1. Going to zero Pose')
        while time_ < zero_duration:
            start_time = time.time()
            time_ += self.control_dt_
            # self.low_cmd.motor_cmd[G1JointIndex.kNotUsedJoint].q = 0  # 1:Enable arm_sdk, 0:Disable arm_sdk
            ratio = np.clip(time_ / zero_duration, 0.0, 1.0)
            self.low_cmd.mode_machine = self.mode_machine_
            self.low_cmd.mode_pr = Mode.PR

            for i, joint in enumerate(self.child2g1_idx_mapping_array):
                self.low_cmd.motor_cmd[joint].mode = 1
                self.low_cmd.motor_cmd[joint].tau = 0.
                self.low_cmd.motor_cmd[joint].q = (1.0 - ratio) * self.low_state.motor_state[joint].q
                self.low_cmd.motor_cmd[joint].dq = 0.
                self.low_cmd.motor_cmd[joint].kp = self.kp_dict[joint]
                self.low_cmd.motor_cmd[joint].kd = self.kd_dict[joint]

            for waist_id, joint in enumerate(self.waist_ind_array):
                self.low_cmd.motor_cmd[joint].mode = 1
                self.low_cmd.motor_cmd[joint].tau = 0.
                self.low_cmd.motor_cmd[joint].q = (1.0 - ratio) * self.low_state.motor_state[joint].q 
                self.low_cmd.motor_cmd[joint].dq = 0.
                self.low_cmd.motor_cmd[joint].kp = self.kp_dict[joint]
                self.low_cmd.motor_cmd[joint].kd = self.kd_dict[joint]

            self.low_cmd.crc = self.crc.Crc(self.low_cmd)
            self.arm_sdk_publisher.Write(self.low_cmd)
            loop_time = time.time() - start_time
            left_time = max(self.control_dt_ - loop_time, 0.0)
            time.sleep(left_time)
            pbar.update(1)

        while not self.child.is_ready:
            print("Waiting for the child...", end='\r')
            if self.shutdown: return
            time.sleep(0.01)

        ## Phase2: Initialize the arm to initial pose
        self.command = initial_command = self.child.get_status()[0]
        # interpolate to initial command
        init_duration = 3.0
        target_qpos = np.concatenate([initial_command['left_leg'],initial_command['right_leg'],initial_command['left_arm'],initial_command['right_arm']])
        time_ = 0
        pbar = tqdm(total=int(init_duration/self.control_dt_), desc='2. Going to init Pose')
        while time_ < init_duration:
            start_time = time.time()
            time_ += self.control_dt_
            self.low_cmd.mode_machine = self.mode_machine_
            self.low_cmd.mode_pr = Mode.PR
            # self.low_cmd.motor_cmd[G1JointIndex.kNotUsedJoint].q = 0  # 1:Enable arm_sdk, 0:Disable arm_sdk
            ratio = np.clip(time_ / init_duration, 0.0, 1.0)
            for i, joint in enumerate(self.child2g1_idx_mapping_array):
                self.low_cmd.motor_cmd[joint].tau = 0.
                self.low_cmd.motor_cmd[joint].q = (1.0 - ratio) * self.low_state.motor_state[joint].q + ratio * target_qpos[i]
                self.low_cmd.motor_cmd[joint].dq = 0.
                self.low_cmd.motor_cmd[joint].kp = self.kp_dict[joint]
                self.low_cmd.motor_cmd[joint].kd = self.kd_dict[joint]

            for waist_id, joint in enumerate(self.waist_ind_array):
                v = self.command['waist'][waist_id] if USE_WAIST else 0.0
                self.low_cmd.motor_cmd[joint].mode = 1
                self.low_cmd.motor_cmd[joint].tau = 0.
                self.low_cmd.motor_cmd[joint].q = (1.0 - ratio) * self.low_state.motor_state[joint].q + ratio * v
                self.low_cmd.motor_cmd[joint].dq = 0.
                self.low_cmd.motor_cmd[joint].kp = self.kp_dict[joint]
                self.low_cmd.motor_cmd[joint].kd = self.kd_dict[joint]
            self.low_cmd.crc = self.crc.Crc(self.low_cmd)
            self.arm_sdk_publisher.Write(self.low_cmd)
            loop_time = time.time() - start_time
            left_time = max(self.control_dt_ - loop_time, 0.0)
            time.sleep(left_time)
            pbar.update(1)

        print("Init pose done, starting teleoperation...")

        iteration = 0
        status_str = "Running... "
        bar_list = ["|", "|", "|", "|", "/", "/", "/", "/", "-", "-", "-", "-", "\\", "\\", "\\", "\\"]
        while not self.child.require_end:
            command = self.child.get_status()
            self.command = command[0]
            target_qpos = np.concatenate([command[0]['left_leg'], command[0]['right_leg'], command[0]['left_arm'], command[0]['right_arm']])
            if self.prev_target_qpos is not None:
                diff = target_qpos - self.prev_target_qpos
                if (abs(diff) > 0.3).any(): break

            start_time = time.time()
            self.low_cmd.motor_cmd[G1JointIndex.kNotUsedJoint].q = 0  # 1:Enable arm_sdk, 0:Disable arm_sdk
            self.low_cmd.mode_pr = Mode.PR
            self.low_cmd.mode_machine = self.mode_machine_
            self.low_cmd.motor_cmd[i].mode =  1 # 1:Enable, 0:Disable
            for i, joint in enumerate(self.child2g1_idx_mapping_array):
                self.low_cmd.motor_cmd[joint].mode = 1
                self.low_cmd.motor_cmd[joint].tau = 0.
                self.low_cmd.motor_cmd[joint].q = target_qpos[i]
                self.low_cmd.motor_cmd[joint].dq = 0.
                self.low_cmd.motor_cmd[joint].kp = self.kp_dict[joint]
                self.low_cmd.motor_cmd[joint].kd = self.kd_dict[joint]
            for waist_id, joint in  enumerate(self.waist_ind_array):
                self.low_cmd.motor_cmd[joint].tau = 0.
                self.low_cmd.motor_cmd[joint].q = 0.0 if not USE_WAIST else self.command['waist'][waist_id]
                self.low_cmd.motor_cmd[joint].dq = 0.
                self.low_cmd.motor_cmd[joint].kp = self.kp_dict[joint]
                self.low_cmd.motor_cmd[joint].kd = self.kd_dict[joint]
            self.low_cmd.crc = self.crc.Crc(self.low_cmd)
            self.arm_sdk_publisher.Write(self.low_cmd)
            loop_time = time.time() - start_time
            left_time = max(self.control_dt_ - loop_time, 0.0)
            time.sleep(left_time)
            iteration += 1
            print(status_str + bar_list[iteration%16], end="\r")
            self.prev_target_qpos = target_qpos

        print("End signal detected.. go back to zero pose")
        zero_duration = 3.0
        time_ = 0
        pbar = tqdm(total=int(zero_duration/self.control_dt_), desc='3. Going back to zero Pose')
        while time_ < zero_duration:
            start_time = time.time()
            time_ += self.control_dt_
            self.low_cmd.motor_cmd[G1JointIndex.kNotUsedJoint].q = 0  # 1:Enable arm_sdk, 0:Disable arm_sdk
            self.low_cmd.mode_machine = self.mode_machine_
            self.low_cmd.mode_pr = Mode.PR
            ratio = np.clip(time_ / zero_duration, 0.0, 1.0)
            for i, joint in enumerate(self.child2g1_idx_mapping_array):
                self.low_cmd.motor_cmd[joint].mode = 1
                self.low_cmd.motor_cmd[joint].tau = 0.
                self.low_cmd.motor_cmd[joint].q = (1.0 - ratio) * self.low_state.motor_state[joint].q
                self.low_cmd.motor_cmd[joint].dq = 0.
                self.low_cmd.motor_cmd[joint].kp = self.kp
                self.low_cmd.motor_cmd[joint].kd = self.kd
            for waist_id, joint in  enumerate(self.waist_ind_array):
                self.low_cmd.motor_cmd[joint].tau = 0.
                self.low_cmd.motor_cmd[joint].q = (1.0 - ratio) * self.low_state.motor_state[joint].q
                self.low_cmd.motor_cmd[joint].dq = 0.
                self.low_cmd.motor_cmd[joint].kp = self.kp_dict[joint]
                self.low_cmd.motor_cmd[joint].kd = self.kd_dict[joint]

            self.low_cmd.crc = self.crc.Crc(self.low_cmd)
            self.arm_sdk_publisher.Write(self.low_cmd)
            loop_time = time.time() - start_time
            left_time = max(self.control_dt_ - loop_time, 0.0)
            time.sleep(left_time)
            pbar.update(1)

        sys.exit(-1)
        return

if __name__ == '__main__':
    ChannelFactoryInitialize(0, 'eth0')
    runner = Runner(device_config)
    runner.Init()
    runner.run()

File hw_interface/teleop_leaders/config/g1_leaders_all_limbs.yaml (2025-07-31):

right_shoulder_pitch_joint:
  ID: 1
  Return_Delay_Time: 1
  Drive_Mode: 1
  Homing_Offset: 2048
  Operating_Mode: 0
  Torque_Enable: 1
right_shoulder_roll_joint:
  ID: 2
  Return_Delay_Time: 1
  Homing_Offset: 0
  Drive_Mode: 1
  Operating_Mode: 0
  Torque_Enable: 1
right_shoulder_yaw_joint:
  ID: 3
  Return_Delay_Time: 1
  Homing_Offset: 0
  Operating_Mode: 0
  Drive_Mode: 1
  Torque_Enable: 1
right_elbow_joint:
  ID: 4
  Return_Delay_Time: 1
  Homing_Offset: 0
  Drive_Mode: 1
  Operating_Mode: 0
  Torque_Enable: 1
right_wrist_roll_joint:
  ID: 5
  Return_Delay_Time: 1
  Homing_Offset: 0
  Operating_Mode: 0
  Torque_Enable: 1
right_wrist_pitch_joint:
  ID: 6
  Return_Delay_Time: 1
  Homing_Offset: 0
  Operating_Mode: 0
  Torque_Enable: 1
right_wrist_yaw_joint:
  ID: 7
  Return_Delay_Time: 1
  Homing_Offset: 0
  Drive_Mode: 1
  Operating_Mode: 0
  Torque_Enable: 1
right/gripper:
  ID: 111
  Return_Delay_Time: 1
  Homing_Offset: 0
  Drive_Mode: 1
  Operating_Mode: 0
  Torque_Enable: 1

left_shoulder_pitch_joint:
  ID: 8
  Return_Delay_Time: 1
  Homing_Offset: 0
  Operating_Mode: 0
  Torque_Enable: 1
left_shoulder_roll_joint:
  ID: 9
  Return_Delay_Time: 1
  Homing_Offset: 0
  Drive_Mode: 1
  Operating_Mode: 0
  Torque_Enable: 1
left_shoulder_yaw_joint:
  ID: 10
  Return_Delay_Time: 1
  Homing_Offset: 0
  Operating_Mode: 0
  Drive_Mode: 1
  Torque_Enable: 1
left_elbow_joint:
  ID: 11
  Return_Delay_Time: 1
  Homing_Offset: 0
  Operating_Mode: 0
  Torque_Enable: 1
left_wrist_roll_joint:
  ID: 12
  Return_Delay_Time: 1
  Homing_Offset: 0
  Operating_Mode: 0
  Torque_Enable: 1
left_wrist_pitch_joint:
  ID: 13
  Return_Delay_Time: 1
  Homing_Offset: 0
  Operating_Mode: 0
  Torque_Enable: 1
left_wrist_yaw_joint:
  ID: 14
  Return_Delay_Time: 1
  Drive_Mode: 1
  Homing_Offset: 0
  Operating_Mode: 0
  Torque_Enable: 1
left/gripper:
  ID: 121
  Return_Delay_Time: 1 
  Homing_Offset: 0
  Drive_Mode: 1 
  Operating_Mode: 0 
  Torque_Enable: 1 

right_hip_pitch_joint:
  ID: 15
  Return_Delay_Time: 1
  Homing_Offset: 0
  Drive_Mode: 1 
  Operating_Mode: 0
  Torque_Enable: 1
right_hip_roll_joint:
  ID: 16
  Return_Delay_Time: 1
  Homing_Offset: 0
  Drive_Mode: 1
  Operating_Mode: 0
  Torque_Enable: 1
right_hip_yaw_joint:
  ID: 17
  Return_Delay_Time: 1
  Homing_Offset: 0
  Operating_Mode: 0
  Drive_Mode: 1
  Torque_Enable: 1
right_knee_joint:
  ID: 18
  Return_Delay_Time: 1
  Homing_Offset: 341
  Operating_Mode: 0
  Torque_Enable: 0

left_hip_pitch_joint:
  ID: 19
  Return_Delay_Time: 1
  Homing_Offset: 0
  Operating_Mode: 0
  Torque_Enable: 1
left_hip_roll_joint:
  ID: 20
  Return_Delay_Time: 1
  Homing_Offset: 0
  Drive_Mode: 1
  Operating_Mode: 0
  Torque_Enable: 1
left_hip_yaw_joint:
  ID: 21
  Return_Delay_Time: 1
  Homing_Offset: 0
  Operating_Mode: 0
  Drive_Mode: 1
  Torque_Enable: 1
left_knee_joint:
  ID: 22
  Return_Delay_Time: 1
  Homing_Offset: 341
  Drive_Mode: 1
  Operating_Mode: 0
  Torque_Enable: 0

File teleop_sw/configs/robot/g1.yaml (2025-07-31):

mesh_dir: 'models/' # Default directory for meshes
robot_cfg:
  name: g1
  asset_cfg:
    asset_dir: ${mesh_dir} # Directory for assets
    urdf_path: 'models/unitree_g1/g1_29dof.urdf' # Path to the URDF file
    xml_path: 'models/unitree_g1/g1_29dof.xml' # If you have xml file, specify the path here or just use urdf file here as well
  ignore_collision_pairs: [] # List of collision pairs to ignore, use * for partial match
  teleop_dt: 0.02
  control_dt: 0.002 # Control loop frequency - 125Hz for PAPRAS
  eef_type: null # Type of end effector: 'hand', 'power_gripper', 'parallel_gripper'
  num_eefs: 4 # number of limbs (end effectors) - 1 for single arm, 2 for dual arm...
  limb_joint_names:
    left_leg:
      - 'left_hip_pitch_joint'
      - 'left_hip_roll_joint'
      - 'left_hip_yaw_joint'
      - 'left_knee_joint'
#      - 'left_ankle_pitch_joint'
#      - 'left_ankle_roll_joint'
    right_leg:
      - 'right_hip_pitch_joint'
      - 'right_hip_roll_joint'
      - 'right_hip_yaw_joint'
      - 'right_knee_joint'
#      - 'right_ankle_pitch_joint'
#      - 'right_ankle_roll_joint'
    left_arm:
      - 'left_shoulder_pitch_joint'
      - 'left_shoulder_roll_joint'
      - 'left_shoulder_yaw_joint'
      - 'left_elbow_joint'
      - 'left_wrist_roll_joint'
      - 'left_wrist_pitch_joint'
      - 'left_wrist_yaw_joint'
    right_arm:
      - 'right_shoulder_pitch_joint'
      - 'right_shoulder_roll_joint'
      - 'right_shoulder_yaw_joint'
      - 'right_elbow_joint'
      - 'right_wrist_roll_joint'
      - 'right_wrist_pitch_joint'
      - 'right_wrist_yaw_joint'
  hand_joint_names:  # No hand for this robot
    left_leg: []
    right_leg: []
    left_arm: []
    right_arm: []
  max_joint_vel: 20.0 # Maximum joint velocity
  world_link: 'pelvis'
  end_effector_link:
    left_leg: left_ankle_roll_link
    right_leg: right_ankle_roll_link
    left_arm: left_rubber_hand
    right_arm: right_rubber_hand
  named_poses:
    #TODO: maybe read this info from srdf file, but conditionally. If not found, use this info
    init: [0,0,0,0,0,0,0,0,0,0,0,0,0,0,0,0,0,0,0,0,0,0]
  viewer_args:
    mujoco:
      azimuth: 172.7000000000001
      distance: 2.6093796441399872
      elevation: -28.550000000000004
      lookat: [-0.21228273,  0.03259374, -0.11615278]
    sapien:
      width: 1510
      height: 768
      fovy: 1.57
      near: 0.1
      far: 100
      pose:
        pos: [ -0.94558, -0.128266, 1.77682 ]
        quat: [ 0.937644, -0.000868946, 0.347589, 0.0023438 ]
    isaacgym:
      cam_pos: [1.41, -0.36, 0.58]
      cam_target: [0.45, -0.23, 0.31]
ik_cfg: # information for inverse kinematics. Use single limb model for each limb.
  # the number of arms in the urdf file, the name of the robot does not matter, but order matters.
  left_leg:
    # chain of joint names from base to end effector
    joint_names: ['left_hip_pitch_joint', 'left_hip_roll_joint', 'left_hip_yaw_joint', 'left_knee_joint']
    ee_link: left_ankle_roll_link
    dt: 0.05
    asset_dir: ${mesh_dir} # Directory for assets
    urdf_path: 'models/unitree_g1/g1_29dof.urdf'
    ik_damping: 0.1
    eps: 1e-3
    base_link: left_hip_pitch_link # base_link in the original urdf file,not the base_link in the ik model

  right_leg:
    joint_names: ['right_hip_pitch_joint', 'right_hip_roll_joint', 'right_hip_yaw_joint', 'right_knee_joint']
    ee_link: right_ankle_roll_link
    dt: 0.05
    asset_dir: ${mesh_dir} # Directory for assets
    urdf_path: 'models/unitree_g1/g1_29dof.urdf'
    ik_damping: 0.1
    eps: 1e-3
    base_link: right_hip_pitch_link # base_link in the original urdf file,not the base_link in the ik model

  left_arm:
    # chain of joint names from base to end effector
    joint_names: ['left_shoulder_pitch_joint', 'left_shoulder_roll_joint', 'left_shoulder_yaw_joint', 'left_elbow_joint', 'left_wrist_roll_joint','left_wrist_pitch_joint', 'left_wrist_yaw_joint']
    ee_link: left_rubber_hand
    dt: 0.05
    asset_dir: ${mesh_dir} # Directory for assets
    urdf_path: 'models/unitree_g1/g1_29dof.urdf'
    ik_damping: 0.1
    eps: 1e-3
    base_link: left_shoulder_pitch_link # base_link in the original urdf file,not the base_link in the ik model

  right_arm:
    # chain of joint names from base to end effector
    joint_names: ['right_shoulder_pitch_joint', 'right_shoulder_roll_joint', 'right_shoulder_yaw_joint', 'right_elbow_joint', 'right_wrist_roll_joint','right_wrist_pitch_joint', 'right_wrist_yaw_joint']
    ee_link: right_rubber_hand
    dt: 0.05
    asset_dir: ${mesh_dir} # Directory for assets
    urdf_path: 'models/unitree_g1/g1_29dof.urdf'
    ik_damping: 0.1
    eps: 1e-3
    base_link: right_shoulder_pitch_link # base_link in the original urdf file,not the base_link in the ik model

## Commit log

2025-08-08 update link to print in two parts
    [G1_Leg_Leader_link_4.1.STL, G1_Leg_Leader_link_4.2.STL, G1_Leg_Leader_link_4.STL]
2025-08-14 update BoM
    [G1_Leg_Leader_link_3.1.STL, G1_Leg_Leader_link_3.2.STL, G1_Leg_Leader_link_3.STL]
2025-08-14 increase tolerance for printing
    [G1_Arm_Leader_L_link_3.STL, G1_Arm_Leader_L_link_4.STL, G1_Arm_Leader_L_link_5.STL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]
